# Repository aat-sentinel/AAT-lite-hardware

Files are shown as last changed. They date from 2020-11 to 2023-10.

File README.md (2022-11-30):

# AAT-lite-hardware
STL and source CAD (google sketchup .skp) for AAT Sentinel lite antenna tracker

Download STL's and source here: https://github.com/aat-sentinel/AAT-lite-hardware/archive/refs/heads/main.zip

User creations are here: https://github.com/aat-sentinel/User-creations-STLs-/archive/refs/heads/main.zip

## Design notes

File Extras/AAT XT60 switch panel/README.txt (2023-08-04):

OLED TYPE 1 - shipped 2021
OLED type 2 - shipped 2022

The files in this folder support type 2. If you have type 1, it may require a modified OLED housing

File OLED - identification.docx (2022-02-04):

Sentinel AAT parts – identifying OLED types

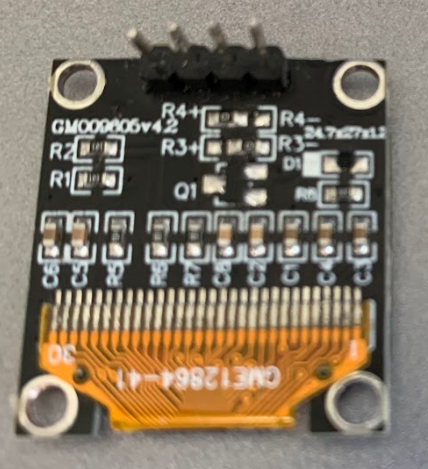
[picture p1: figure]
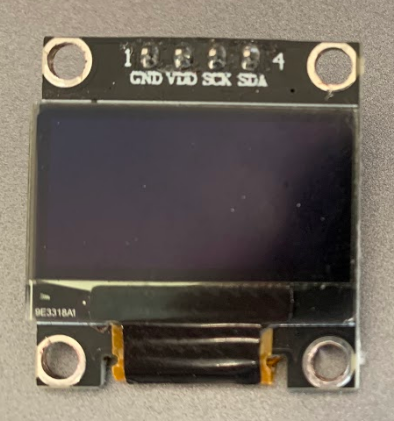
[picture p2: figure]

Type 1 3mm holes

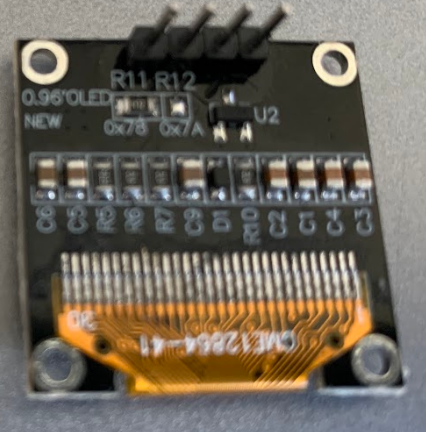
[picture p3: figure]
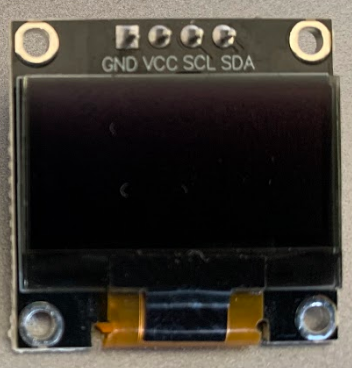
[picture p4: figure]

Type 2 2mm holes

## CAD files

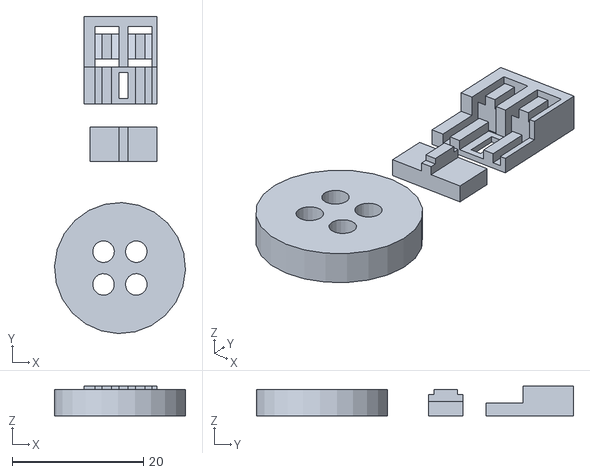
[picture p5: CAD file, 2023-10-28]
LED assembly jig.stl
20.0 x 48.4 x 4.54

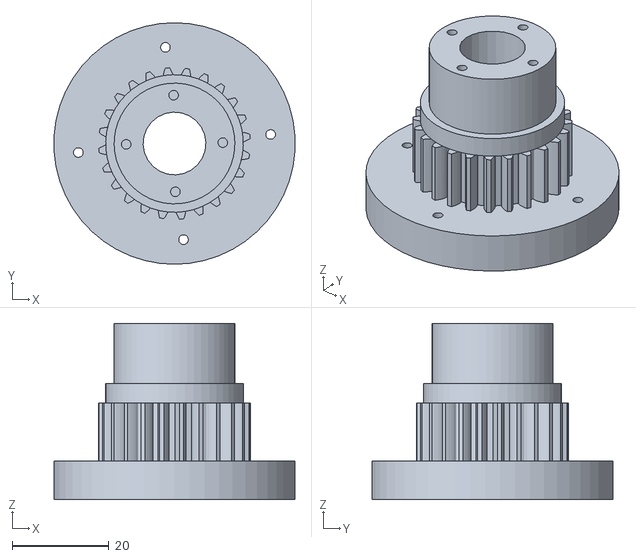
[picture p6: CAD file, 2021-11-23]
Gears - main shaft.stl
49.9 x 50.0 x 36.5

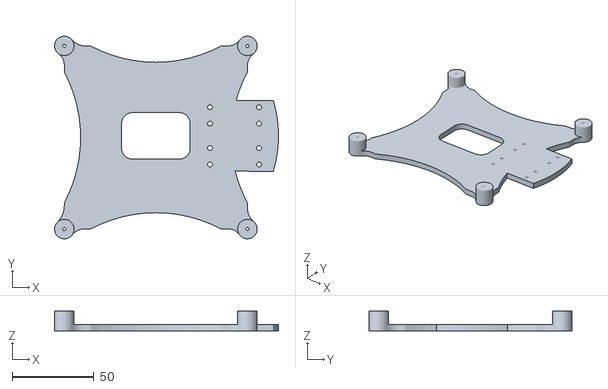
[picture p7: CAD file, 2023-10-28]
Extras/AAT 150mm dual Triple feed patch mount/150mm mount.stl
137.0 x 124.0 x 12.0

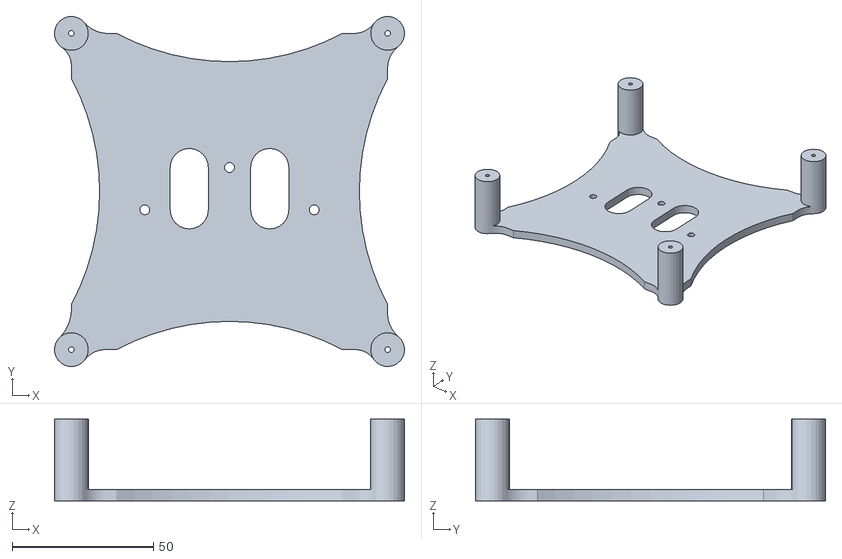
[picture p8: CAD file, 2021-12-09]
Extras/AAT 150mm Triple feed patch mount/150mm triple feed patch - antenna.stl
124.0 x 124.0 x 29.0

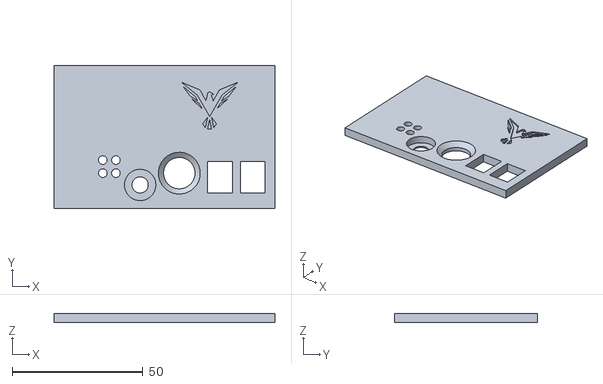
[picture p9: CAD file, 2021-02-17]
Extras/AAT basic panel/Box - panels front .stl
84.4 x 54.6 x 3.60

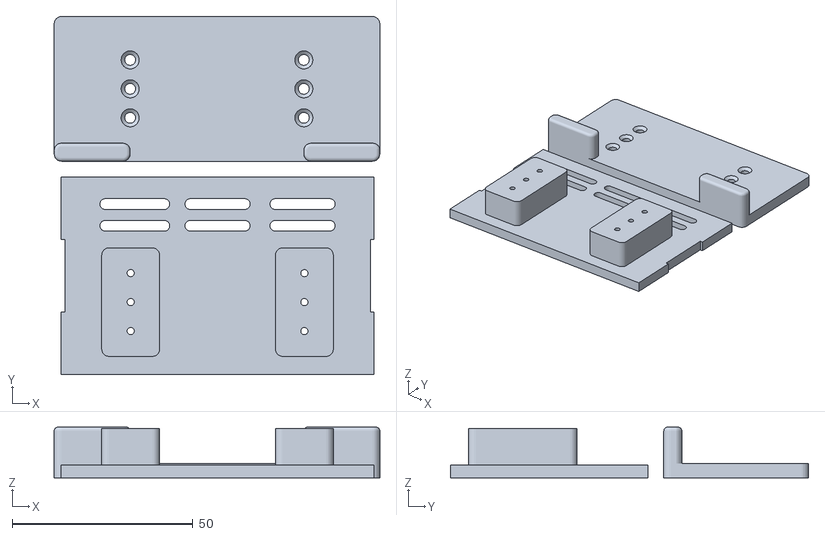
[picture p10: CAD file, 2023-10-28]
Extras/AAT battery panel mount/AAT battery panel mount.stl
90.0 x 98.9 x 14.0

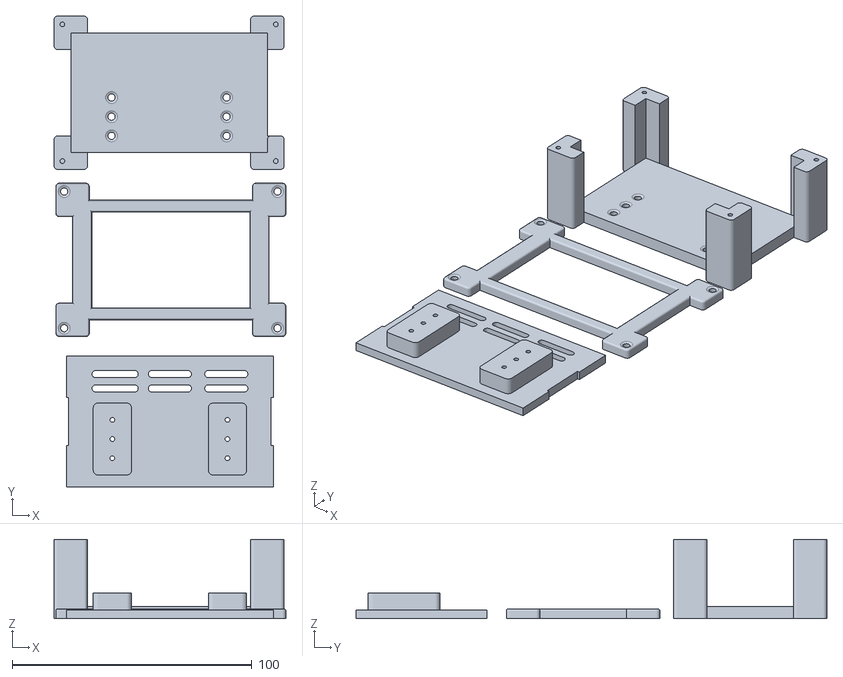
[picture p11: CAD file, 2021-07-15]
Extras/AAT IRC Powerplay panel mount/AAT IRC Powerplay panel mount.stl
96.7 x 196.4 x 33.0

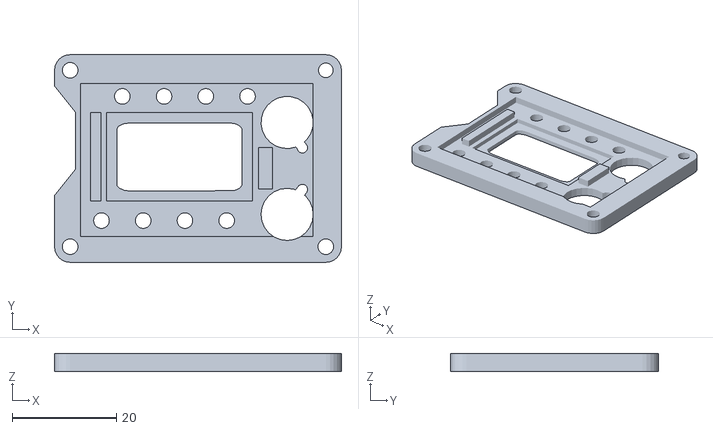
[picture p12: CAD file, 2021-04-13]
Extras/AAT RX mount - Eachine Pro58/Eachine Pro58 mount fascia.stl
55.0 x 39.8 x 3.50

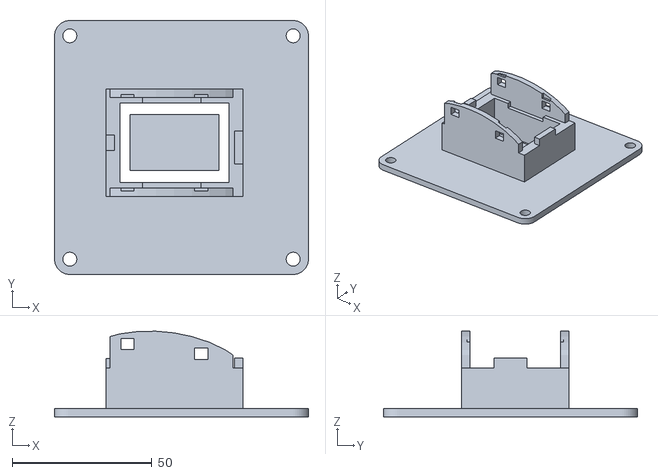
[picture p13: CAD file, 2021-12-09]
Extras/AAT RX mount - generic FATSHARK/AAT RX mount - FATSHARK.stl
91.0 x 91.0 x 30.7

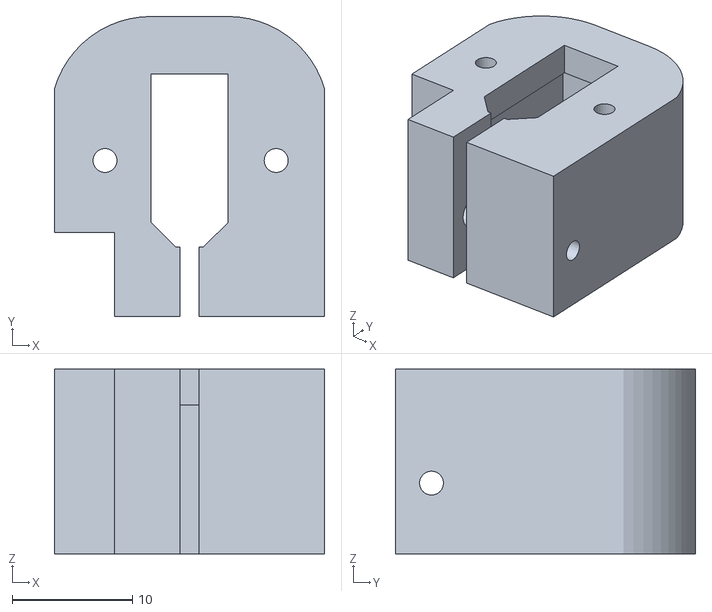
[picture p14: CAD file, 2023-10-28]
Extras/AAT XT60 switch panel/XT60 panel connector.stl
22.5 x 25.0 x 15.4

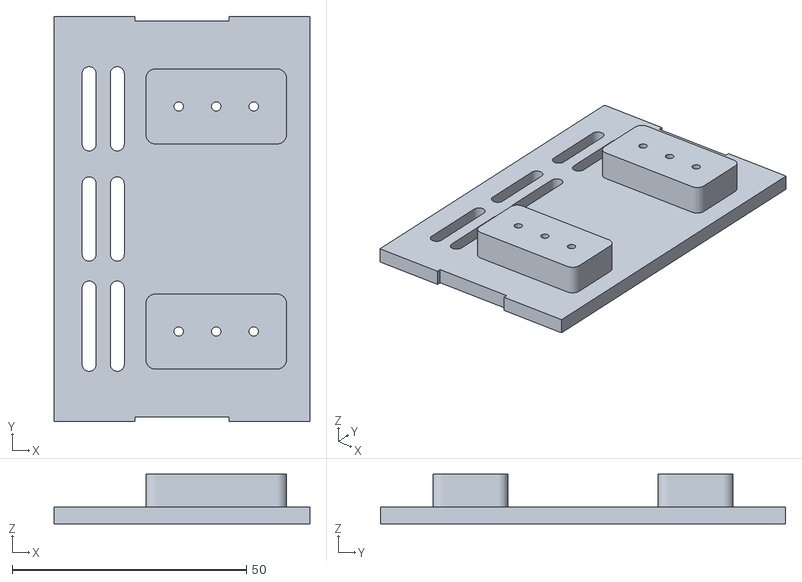
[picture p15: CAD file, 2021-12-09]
Extras/AAT-FPV JAPAN DVR mount/AAT FPV DVR mount panel.stl
54.6 x 86.4 x 10.6

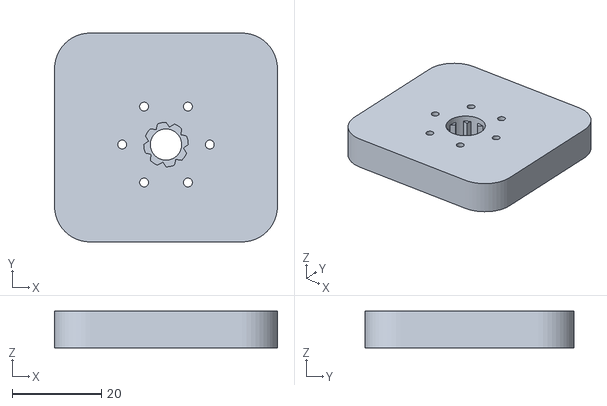
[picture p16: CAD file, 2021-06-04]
Extras/AAT-tripod thread mount/AAT-tripod thread mount.stl
50.0 x 46.8 x 8.25

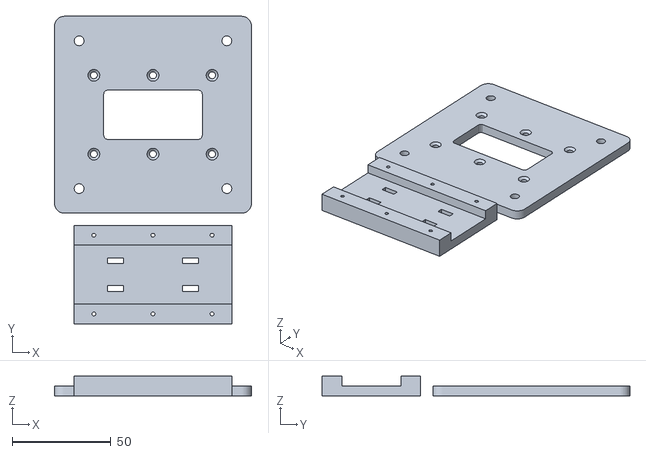
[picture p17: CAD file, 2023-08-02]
Extras/Other/FPV tripod 10 inch LCD mount/FPV tripod 10 inch LCD mount.stl
100.0 x 156.1 x 10.0

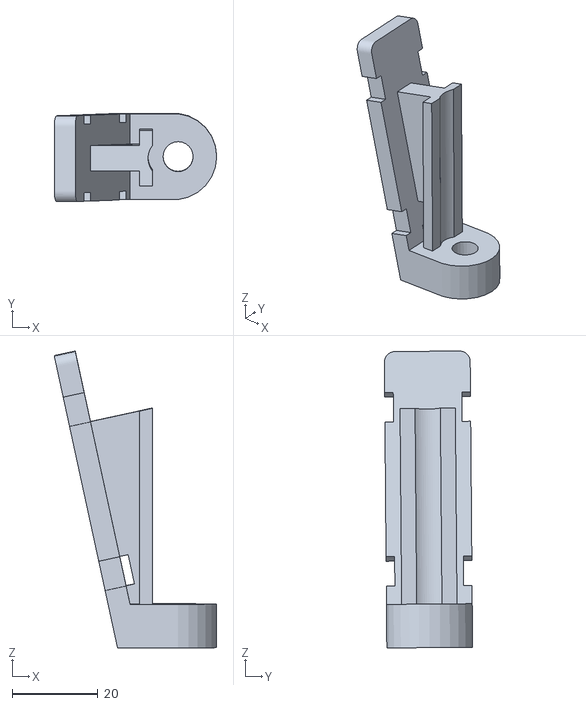
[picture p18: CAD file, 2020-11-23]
Extras/Other/FPV tripod 7 inch LCD mount/FPV tripod 7 inch LCD mount.stl
37.9 x 20.6 x 69.2

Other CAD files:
Extras/Other/FPV tripod battery mount/FPV tripod battery mount smoothed.stl
Extras/Other/FPV tripod cable retainer/FPV tripod cable retainer.stl
Extras/Other/FPV tripod goggles rest/FPV tripod goggles rest.stl
Extras/Other/FPV tripod GoPro mount/FPV tripod GoPro mount.stl
Bearing retainer - inner.stl
Bearing retainer - outer.stl
Box - base.stl
Box - gear cover.stl
Box - panels front with OLED type 1.stl
Box - panels front with OLED type 2.stl
Box - panels front with OLED.stl
Box - panels rear.stl
Box - panels side.stl
Box - top.stl
Extras/AAT 150mm Triple feed patch mount/150mm triple feed patch - antenna.skp
Extras/AAT 150mm Triple feed patch mount/150mm triple feed patch - plate.skp
Extras/AAT 150mm Triple feed patch mount/150mm triple feed patch - plate.stl
Extras/AAT 150mm dual Triple feed patch mount/150mm mount plate.skp
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

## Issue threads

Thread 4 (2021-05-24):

Please provide "Box - panels battery mount" as two seperate parts

jasc76, 2021-05-24:
I cant get them separated in Fusion....

ShikOfTheRa, 2021-05-24:
Yes this no problem. I will do that first thing tomorrow

ShikOfTheRa, 2021-05-25:
Seperated:

https://github.com/aat-sentinel/AAT-lite-hardware/tree/main/Extras/AAT%20battery%20panel%20mount

Closed 2021-05-26.

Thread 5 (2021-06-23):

Pan Issue

Davierooker, 2021-06-23:
Hi, I've built and tested my tracker and when it works it is really good. However more often than not the pan stays facing North, although the tilt appears to be working. I've tested the pan in the simulator and it works as expected, so I'm not sure what is going on. The tracker appears to be getting telemetry OK because the tilt appears to working. I'm arming the plane next to the tracker, so don't know what else to try.

ShikOfTheRa, 2021-06-24:
@whammer007

This is a really strange one – works ok in simulator, but intermittent yaw only in flight.
This makes we think the flight controller must be sending data if the tilt is working – but almost sounds like it is sending wrong yaw info.
I am wondering if something has become an issue in iNAV during the changes up to the final 3.0 release version.

If you are able to save a log file as error414 indicated on RCG it would be most valuable in helping identify the cause…

What version iNav (assume that’s what is used)
What FC
Could you post a CLI dump

Davierooker, 2021-06-24:
I did some more testing and found that sometimes the pan servo does not respond in the simulator, then after a power cycle responds properly. I carried out further testing as below:
I powered up the tracker and checked the servo operation was OK in the simulator. I then powered up the plane and waited for telemetry. I armed the plane and moved it beyond 10 metres. I repeated this 10 times. I have found that if the servo moves in the simulator, then it will track correctly.
I am using INAV 3.0 release version on various Matek FC's in this case an F411wse.
I was unable to retrieve the tracker log as yet, but the signal strength was constant and the angle values were changing (even when not panning correctly).
I have attached the FC diff, although I'm not sure that it is INAV related...
[Drift 3.0.txt](https://github.com/aat-sentinel/AAT-lite-hardware/files/6708944/Drift.3.0.txt)

ShikOfTheRa, 2021-06-24:
OK - helps a lot. I was really worried something changed in iNav.
I think what you have said rules that out. Angles changing and also seeing it fail on the sim helps validate.

As it is same power supply for both servos, I think it is worth looking at these next:
- Check servo voltage is OK - approx 5v
- Bad servo wire / crimp connector joint
- Bad solder joint on the pan servo pin header
- Bad servo
- Cracked PCB track - Atmega IC / Supply / GND to servo pin
- Bad solder joint on Atmega IC pin driving servo ( unlikely / unlucky)

If could check the first 3 and no fix I would be happy to send out another servo.

Great testing and many thanks for your time helping to diagnose.

ShikOfTheRa, 2021-06-24:
Completely off topic - what are you thoughts on the drifter? I have always wanted to try a glider and it seems quite a good option for the calm days

Davierooker, 2021-06-24:
The Drift is a cracking model, it flies really well. I run it with a 2S lion pack and it will fly for an hour. It can handle a bit of wind as well.

ShikOfTheRa, 2021-06-24:
I'm tempted... I have a strix mini goblin running 2s and really like that one so it seems quite a good option.

ShikOfTheRa, 2021-06-24:
Can you drop me an email @virtualpilot and I'll get a servo out to you. It seems most likely issue

Davierooker, 2021-06-24:
I've checked the board for any damage (none) and decided to reflow the servo pins, I will test again tomorrow if the rain ever goes off. I have a spare MG995 servo that I can swap out to further troubleshoot if required. Thanks for all your help so far, I'll keep you posted.

ShikOfTheRa, 2021-06-24:
Cheers!

The pan servo needs to be able to support 180 deg - so if yours doesn't could possibly swap the tilt servo to the pan position. If need one happy to send out.

Davierooker, 2021-06-25:
Some follow up and test results from today.
I reflowed the servo headers - no change.
I replaced the servo with an identical brand new one I had - no change.
The next time it failed to pan, I power cycled the tracker and it immediately tracked straight at the target. So it would appear that this is at worst only a minor annoyance if it is cured by a power cycle of the tracker after launch. ( I was definitely overthinking this as I'm used to the U360GTS tracker which has way to many things that can go wrong and can be immensely frustrating to get right).
 One thing I did notice while testing was, occasionally when arming the "arm screen" on the video feed would not come up. (the plane would still arm) when this happened the tracker did not track AT ALL. The way to tell if it "sees" the plane is armed is that the Telemetry LED blinks once when the arm switch is triggered, if it stays solid while the arm switch is operated then it will not track. (but the plane will still arm) This definitely seems like an INAV issue, which is also resolved by power cycling the tracker so all good.
Thanks for your support.

ShikOfTheRa, 2021-06-25:
Thanks again for the the testing.

In all the time I have been flying I've never seen that issue or had to power cycle for servos. The only time I have had to do that is if I have changed planes where one was say NTSC and the other PAL. I think it works anyway if leave long enough.

The iNav one sounds interesting....
The blip is because Telemetry is not sent when armed screen is shown. This is expected.
No arming screen - I don't pay much attention to it really. I will install v3 on on my test copter and see what it does...
But if cycling the tracker fixes that - weird. Makes it not look like an iNav issue.

We'll keep looking at it from this end to see if can identify anything odd in iNav.

Davierooker, 2021-06-27:
I managed to get some actual flight tests done yesterday, and the results were not good to say the least. The first and the last flight tracked perfectly, however the 20 or so launches in between resulted in no pan. The tilt was working on all flights, but not the pan. I tried the power cycle trick in flight, but that did not work at all. The heading on the display is about right and is changing as the plane flies around, but there is no response from the pan servo. It is receiving power as it is locked in the North position and resistance can be felt if I try to turn it.

ShikOfTheRa, 2021-06-28:
Out of interest - can you advise what version firmware you are running on the board? Is it the one shipped with the board?
I am running 3.2.2 on mine which is the latest

Davierooker, 2021-06-28:
I'm running 3.2.2 as well.

ShikOfTheRa, 2021-06-29:
I am completely puzzled by this one!

If blue light is on it is receiving valid tracking info. There is error checking to verify data received is same as sent.
If data is corrupt or no telemetry received, blue light goes out quickly.

Heading and tilt is sent in the same data packet, so if tilt is moving OK, it must be receiving heading info to too.
It is possible iNav is sending incorrect incorrect data. But...

Heading data is shown to be changing on the OLED display - so it seems that iNav is sending correct heading data and tracker is receiving heading data and also processing it to be able to display.

The pan / tilt uses same supply and as the pan servo seems locked it sound like it is receiving power and ground
This points towards an issue with the servo / servo drive code / servo drive circuit.
Servo replaced- so unlikely to a second one has same issue.

And flying with a different FC worked....
Seems no logic to how this is working/not working. Truly stumped.

If we need to do this to eliminate PCB this might be next option, but it doesn't seem like a hardware issue with PCB.
Still trying to work though failure modes that would cause this...

Davierooker, 2021-06-29:
Thanks for your help on this, it's really appreciated. I took the Drift back out this morning as the weather was great...no pan. I power cycled it a couple of times and it started panning. This happened for the 3 flights that I had. This is the model F411WSE FC that seems to be having the issue. I will report back any other findings with different FC's etc. as I fly them.

ShikOfTheRa, 2021-06-29:
If the telemetry led is on, it should mean that the FC is sending data tracker can understand.
And if heading display changes and the power cycle fixes it mid flight it sounds like data sent is correct.
Working tilt supports this theory

I would expect if problem with the FC that the telemetry LED would not light at all. Also no tilt.

Let us know how the other boards work. I cannot think how The FC would only affect pan operation

ShikOfTheRa, 2021-07-23:
Hi - did you have any further results from testing?

We have been unable to replicate this issue with the equipment we have but I have a couple of questions:
1 - what camera(s) do you use
2 - do you use dual camera input on the WSE ?

Davierooker, 2021-07-23:
Hi,
I've had a few flights with different FC's and cameras which I will summarize below:

ZOHD Drift, Matek F411WSE, Runcam Split 3 lite = Very hit and miss with tracking.
ZOHD Dart, Matek F411 WSE, Caddx Starlight = Tracks OK.
Ranger 1600, Matek F722STD, Runcam Split 2 = Tracks OK
Mini Talon, Matek F405 Wing, Caddx Tarsier = Tracks OK
Vortigaunt, Matek F765 Wing, Caddx Tarsier = Tracks OK

With the exception of the drift, the models above have only been flown a handful of times so far.

Its kinda looking like the camera/video feed from the Runcam Split 3 lite setup?
I will test the drift with a different camera in it and feed back the results.

I have not used the dual input of the WSE.

ShikOfTheRa, 2021-07-23:
Thanks for the feedback. As you say its helping narrow it down a little.

This is just a possibility I was thinking about last night…

During development of MWOSD I had issues with a few cameras that power up in one mode then changed to another  - usually NTSC before changing to PAL. This caused many issues because it detected NTSC signal so presumed it was an NTSC camera.
The solution was to keep checking the signal and then change if necessary.

With the tracker it is not so easy to do this as it is not always a clean video signal.  Have to take into consideration poor  signal / loss of signal  and determining valid data which itself takes a few seconds. Not what you want at extremes or range!

So suggestions for now for the Split 3are are:
1 Always restart the tracker after the aircraft powered up and stabilised.
2 Always have a good clean power feed to camera / VTX – this also can impact the telemetry.

We are looking at options to help mitigate this in software. It will take some time with plenty of testing by us first as it would be a change to the core telemetry capturing which has been tuned over the last 24 months. .

Worst case scenario - will have to get one to evaluate as this is the only such report we have recieved.

ShikOfTheRa, 2021-08-07:
Can you try beta firmware here with your spilt camera?
It may help the issue..
https://github.com/aat-sentinel/AAT-lite-firmware

Davierooker, 2021-08-07:
I'll give it a go as soon as the weather clears up.

ShikOfTheRa, 2021-09-24:
Hello - just wondered if you ever had opportunity to test?

Davierooker, 2021-09-24:
I've only had a handful of flights on the new firmware, so didn't think it was enough to report back. I did fly the "problem" model however and had no issues.

ShikOfTheRa, 2021-09-27:
OK, no problem. I'll keep this open for now. Thanks for feedback and testing!

Davierooker, 2021-11-13:
I managed to get 4 flights in today with 2 different models, no issues at all.

ShikOfTheRa, 2021-11-15:
Awesome. I t seems @error414 has added a fix and improvement at same time.

Closed 2022-02-06.

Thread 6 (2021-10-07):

Gears - servo.stl and skp issue

CADavebert, 2021-10-07:
There is an issue with the STL file, as well as the sketchup file.

The solid bits of the center of the gear are missing.

Closed 2022-02-06.

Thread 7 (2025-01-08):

error in stl

Rothammel, 2025-01-08:
cura says areas are missing here

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

ShikOfTheRa, 2025-01-08:
Updated files - can you try again and advise?

Rothammel, 2025-01-08:
awesome, good work

Closed 2025-01-08.

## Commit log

2020-11-27 Battery mount option
    [Box - panels battery mount.skp, Box - panels battery mount.stl]
2020-11-30 Add XT60
    [XT60 M to XT60 F inline switch.skp, XT60 M to XT60 F inline switch.stl, XT60 to DC 5.5 inline switch.skp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]
2021-02-17 Update dbox
    [Box - top.skp, Box - top.stl]
2021-04-13 Updated STL and source
    [Bench rest - QR.skp, Bench rest - QR.stl, Box - panels LCD.skp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]
2021-04-13 Revert "Updated STL and source"
    This reverts commit e33bad276f471acd93dc3ec245aaf6e1c4e7a129.
    [Bearing retainer 6005 - outer.skp, Bench rest - QR.skp, Bench rest - QR.stl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]
2021-05-21 Eachine mount added
    [Bearing retainer 6005 - outer.skp, Bearing retainer 6005 - outer.stl, Box - top 6005x1.skp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]
2021-05-25 AAT battery panel mount split components
    [AAT battery mount - mount.stl, AAT battery mount - panel.stl, AAT battery panel mount.skp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]
2021-06-04 Added standard threaded tripod mount option
    [Mount - threaded.skp, Mount - threaded.stl]
2021-07-15 Added IRC mount and led jig
    [AAT IRC Powerplay panel mount.skp, AAT IRC Powerplay panel mount.stl, LED jig.skp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]
2021-09-03 XT 60 panel with switch option
    [Box - panels front with XT60.skp, Box - panels front with XT60.stl, XT60 panel connector.skp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]
2021-10-08 fix servo gears
    [Gears - servo.skp, Gears - servo.stl]
2021-11-23 STL improvements
    Increased servo clearance
    Camera thread insert added to HAMA QR adapter
    Locating pegs added to Box base and top for orientation
    LED jig resized. Previous was incorrect
    [Box - base.skp, Box - base.stl, Box - top.skp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]
2021-11-23 Change sketchup version for servos
    Converted to SketchUp Make 17.2.2555
    [Box - panels front .skp, Box - panels front .stl, Gears - servo.skp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]
2021-12-09 Additional extras added
    [150mm triple feed patch - antenna.skp, 150mm triple feed patch - antenna.stl, 150mm triple feed patch - plate.skp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]
2021-12-11 Improved tilt arm bearing mount
    [Tilt - arms.skp, Tilt - arms.stl]
2022-02-04 oled update
    [Box - panels front OLED type 1 with XT60.skp, Box - panels front OLED type 1 with XT60.stl, Box - panels front with OLED type 1.skp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]
2022-02-06 OLED changes
    [Box - panels front with OLED type 1.skp, Box - panels front with OLED type 1.stl, Box - panels front with OLED type 2.skp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]
2022-04-01 Added OLED with switch support for batch 3 trackers
    [Box - panels front OLED type 2 with XT60 part 1.skp, Box - panels front OLED type 2 with XT60 part 1.stl, Box - panels front OLED type 2 with XT60 part 2.skp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]
2022-06-17 Updated box-top to support new OLED
    [Box - top.stl]
2022-07-01 Corrected hole sizes
    [Bearing retainer - outer.skp, Bearing retainer - outer.stl]
2022-07-04 Update Bearing retainer - outer.skp
    [Bearing retainer - outer.skp]
2022-07-04 Update Bearing retainer - outer.stl
    [Bearing retainer - outer.stl]
2023-08-02 Minor changes - rounding etc.
    [Box - panels front OLED type 1 with XT60.skp, Box - panels front OLED type 1 with XT60.stl, FPV tripod 10 inch LCD mount.skp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]
2023-08-04 Updated OLED XT60 panel to match design of standard
    [Box - panels front OLED type 2 with XT60 part 1.skp, Box - panels front OLED type 2 with XT60 part 1.stl, Box - panels front OLED type 2 with XT60 part 2.skp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]
2023-10-28 Updates and added dual 150mm mount
    [150mm mount plate.skp, 150mm mount plate.stl, 150mm mount.skp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]
2023-10-30 Added Goggles tripod rest
    [FPV tripod FPV goggles rest.skp, FPV tripod FPV goggles rest.stl]
2023-11-27 Updated tripod goggles rest
    [FPV tripod FPV goggles rest.skp, FPV tripod FPV goggles rest.stl, FPV tripod goggles rest.skp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]
2024-06-21 FPV tripod goggles rest
    Increased from single to triple joint for extra strength
    [FPV tripod goggles rest.skp, FPV tripod goggles rest.stl]
2025-01-08 Mount plate update
    [Tilt - mount plate.skp, Tilt - mount plate.stl]
2026-03-31 Revise README with documentation and download links
    Updated README to include user guides, assembly manual, and firmware links.
